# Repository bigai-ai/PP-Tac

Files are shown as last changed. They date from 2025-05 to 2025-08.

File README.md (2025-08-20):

# PP-Tac: Paper Picking Using Tactile Feedback in Dexterous Robotic Hands

[Pei Lin<sup>*</sup>](http://peilin-666.github.io/)<sup>1,2</sup>,
[YuZhe Huang<sup>*</sup>]<sup>1,3</sup>,
[Wanlin Li<sup>*</sup>](https://mrliwanlin.github.io/)<sup>1</sup>,
[Jianpeng Ma]<sup>1</sup>,
[Chenxi Xiao<sup>†</sup>](https://scholar.google.com/citations?hl=zh-CN&user=Qhiy3doAAAAJ)<sup>2</sup>,
[Ziyuan Jiao<sup>†</sup>](https://scholar.google.com/citations?user=YfWhJZoAAAAJ&hl=zh-CN&oi=ao)<sup>1</sup>

<sup>1</sup>Beijing Institute for General Artificial Intelligence,
<sup>2</sup>ShanghaiTech University,
<sup>3</sup>Beihang University

# R-Tac Sensor Guide
### Low-cost, 120fps, Round-shape Single-channel Vision-based Tactile Sensor
[[Project page]](https://peilin-666.github.io/projects/PP-Tac/)
[[Paper]](https://arxiv.org/abs/2504.16649)
[[Video Tutorial_Youtube]](https://www.youtube.com/watch?v=-npk0cRKWGI)
[[Video Tutorial_Bilibili]](https://www.bilibili.com/video/BV1pLKwzkEMb/?spm_id_from=333.337.search-card.all.click)

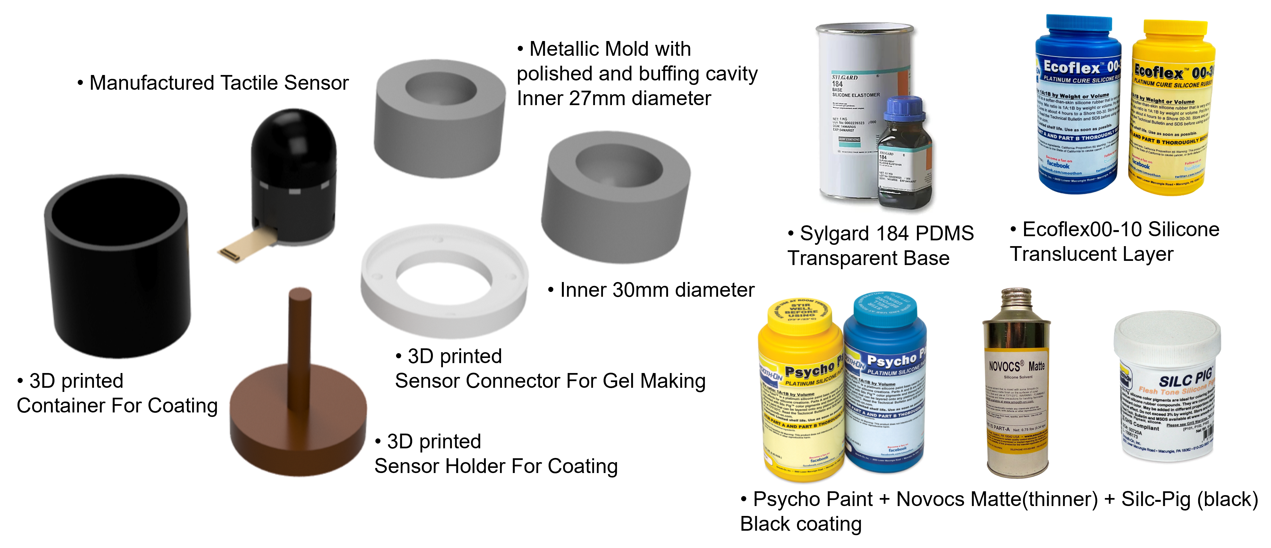
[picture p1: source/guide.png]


## CAD Models</a>
All CAD models can be downloaded and edited from [[onshape]](https://cad.onshape.com/documents/9472112f26da7f3a688b4739/w/3c5ca2de4889759493b1cc6c/e/c49e7e8ea4181ab75b1e7674)
(right click and copy link address to enter).<br>
3D printed files (print with supportings) can be found in [3Dprinting](Model/3Dprinting).

## Camera</a>
We use 120fps OV9281 Monochrome camera module which can be bought from [Taobao](https://item.taobao.com/item.htm?id=740654464379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) or [Amazon](https://www.amazon.co.uk/Global-Shutter-Camera-Detection-Modules-100-degrees/dp/B0D5SNTHSD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)

## PCBs</a>
The PCB files can be downloaded from [PCB](PCB/) and is powered by 5V.<br>
If you opt for white LED chips, it is recommended to select the 2835 package type and pay attention to the anode and cathode of the LED chips.<br>
<div style="display: flex; align-items: center;">
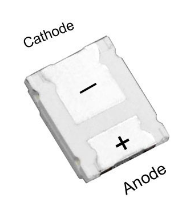
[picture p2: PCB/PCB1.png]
  
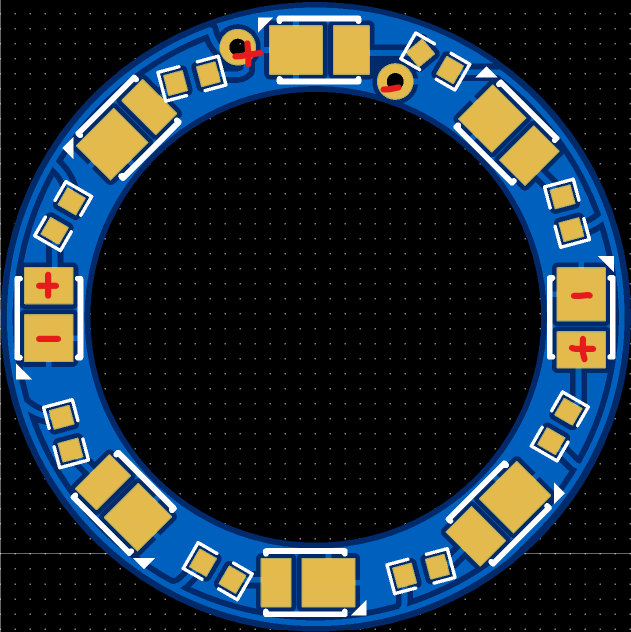
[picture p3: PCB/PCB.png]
  
</div>

## Diffuser Boards</a>
Diffuser patterns (.dxf) can be downloaded from [Diffuser](Model/Diffuser). It is recommended to laser-cut the [double-sided frosted one](https://detail.tmall.com/item.htm?id=550079594688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). You can also try 3D printing with white resin. <br>

## Metallic Mold</a>
The design files can be downloaded from [Mold](Model/MetalMold). Two molds are needed for PDMS casting (27mm diameter) and Silicone casting (30mm diameter). The mold is fabricated using stainless steel with polished and buffing cavity.<br>

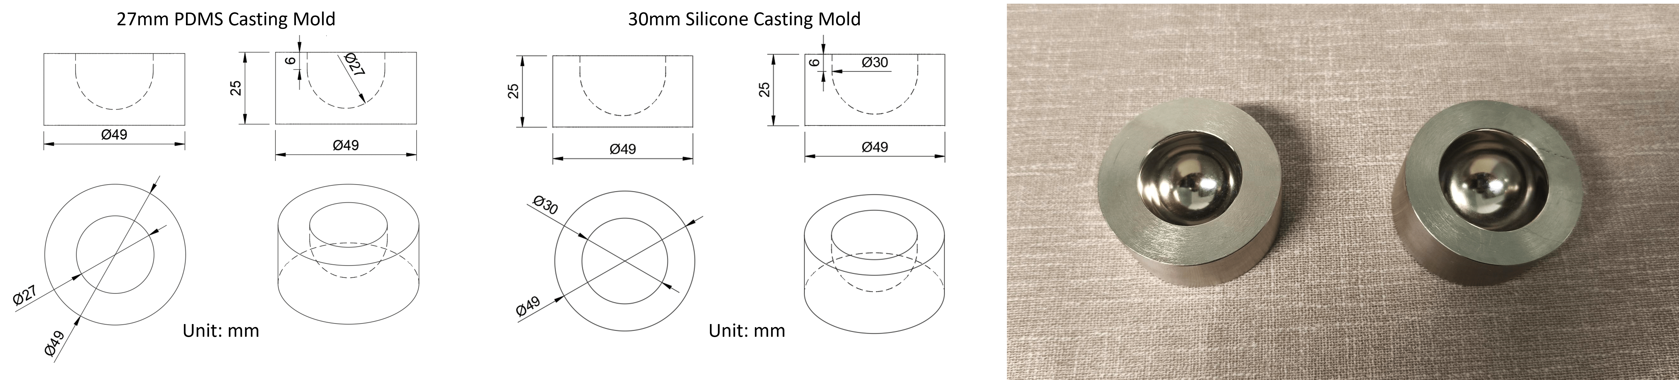
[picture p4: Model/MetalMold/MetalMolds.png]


## BOM</a>

| Component | Description | Remark |
|---|---|---|
| PDMS | Transparent base | [SYLGARD™ 184](https://www.dow.com/en-us/pdp.sylgard-184-silicone-elastomer-kit.01064291z.html#overview) |
| Silicone | Translucent layer | [Ecoflex™ 00-10](https://www.smooth-on.com/products/ecoflex-00-10/) |
| Black pigment | Coating colorant | [Silc Pig™](https://www.smooth-on.com/products/silc-pig/) |
| Coating | Coating layer | [Psycho Paint™](https://www.smooth-on.com/products/psycho-paint/) |
| Thinner | Coating layer thinner | [NOVOCS™ Matte](https://www.smooth-on.com/products/novocs/) |
| Release agent | Silicone release agent | [Ease Release™ 200](https://www.smooth-on.com/products/ease-release-200/) |
| Bolts | M2 * 4 & M1.6 * 5 & M3 *4 | bolts |
| Hot melt nuts | M2 * 2 * 3 | nuts |
| Soldering iron | Compatiable with above nuts | [Soldering Iron](https://item.taobao.com/item.htm?_u=i2jo70qs4f40&id=676644094694&spm=a1z09.2.0.0.32402e8dfa9bP4)|
| Scale | For silicone mixing | Electronic Scale |
| Tape | Double-sided tape | Tape |
| Stick | Stirring silicone | Small Wood Stick |
| Cup | Container for silicone | Disposable Cups |
| Sticker | Dust removal of silicone surface | [Sticker](https://item.taobao.com/item.htm?_u=i2jo70qsf114&id=561103645534&spm=a1z09.2.0.0.32402e8dfa9bP4)|
| Vacuum pump | Air degassing for silicone | [Vacuum Pump](https://detail.tmall.com/item.htm?id=593806957297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)|
| Other tools | Small scissor, tweezer, knife | Tools |

## Video Guide</a>
[[YouTube]](https://www.youtube.com/watch?v=-npk0cRKWGI)
[[Bilibili]](https://www.bilibili.com/video/BV1pLKwzkEMb/?spm_id_from=333.337.search-card.all.click)

# Sensor Calibration
**Recommended camera resolution: 640 * 480**
## 0. Camera Intrinsic Calibration</a>
Refer to [this website](https://github.com/dyfcalid/CameraCalibration/tree/master/IntrinsicCalibration) for intrinsic calibration.
## 1. Camera Extrinsic Calibration</a>
3D print the [calibration tools](Calibration/3Dprint): top, surrounding and 5 pins. Drill and clean the holes in the top model to ensure that pins can be inserted.<br>

In accordance with the hole index in the figure below and referring to the **capture name** in this [folder](Calibration/sensor1/calib_extrinsic), insert the five pins into the corresponding holes in one go. Subsequently, save and replace the existing images.
<div style="display: flex; align-items: center;">
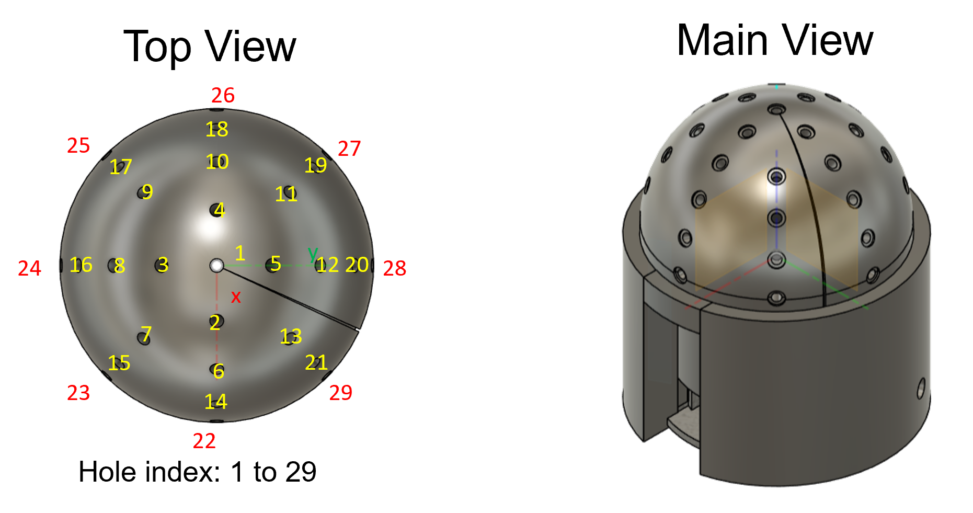
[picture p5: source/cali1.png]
  
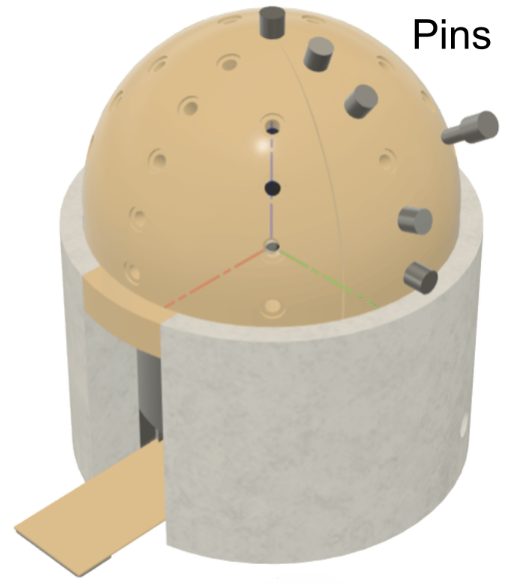
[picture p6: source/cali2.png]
  
</div>

run ./Calibration/1CameraExtrinsics.py and replace the **CAMERA_MATRIX** and **Distortion** with your own camera intrinsc parameters to obtain the camera extrinsics.

## 2. Obtain the Reference Depth Map</a>
run ./Calibration/2Reprojection.py to obtain the reference depth map and the mask center and radius.

## 3. Surface Reconstruction</a>
you can either directly run ./Calibration/3ShapeReconstruction_directuse.py to obtain the surface shape via the model we have trained using indenters 
<br>
or 
<br>
you can build a table by yourself using a single ball capture (press on the top middle area), by running ./Calibration/3SensorCalibration.py and ./Calibration/4ShapeReconstruction.py

## Acknowledgment</a>
[9DTact: A Compact Vision-Based Tactile Sensor for Accurate 3D Shape Reconstruction and Generalizable 6D Force Estimation](https://arxiv.org/abs/2308.14277), Lin et al., RAL 2023

## Reference
```
@article{lin2025pp,
  title={PP-Tac: Paper Picking Using Tactile Feedback in Dexterous Robotic Hands},
  author={Lin, Pei and Huang, Yuzhe and Li, Wanlin and Ma, Jianpeng and Xiao, Chenxi and Jiao, Ziyuan},
  journal={arXiv preprint arXiv:2504.16649},
  year={2025}
}
```

<!-- 
```
@INPROCEEDINGS{lin2025pp, 
    author={Lin, Pei and Huang, Yuzhe and Li, Wanlin and Ma, Jianpeng and Xiao, Chenxi and Jiao, Ziyuan},
    title     = {PP-Tac: Paper Picking Using Tactile Feedback in Dexterous Robotic Hands},
    booktitle = {Robotics Science and Systems (RSS)}, 
    year      = {2025}, 
} 
```
-->

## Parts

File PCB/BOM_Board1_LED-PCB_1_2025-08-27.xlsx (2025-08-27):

No. | Quantity | Comment | Designator | Footprint | Value | Manufacturer Part | Manufacturer | Supplier Part | Supplier
1 | 8 | HL-AM-2835H421W-S1-08-HR6(SDCM | LED1,LED2,LED3,LED4,LED5,LED6,LED7,LED8 | LED-SMD_L3.5-W2.8-RD |  | HL-AM-2835H421W-S1-08-HR6(SDCM | HONGLITRONIC(鸿利光电) | C516134 | LCSC
2 | 8 | 470Ω | R1,R2,R3,R4,R5,R6,R7,R8 | R0603 | 470Ω | 0603WAF4700T5E | UNI-ROYAL(厚声) | C23179 | LCSC

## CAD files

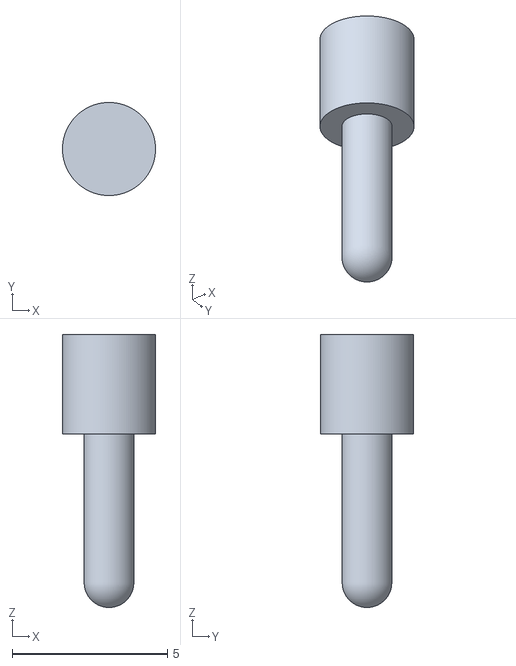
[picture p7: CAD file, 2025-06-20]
Calibration/3Dprint/calibration_5pins.stl
3.00 x 3.00 x 8.80

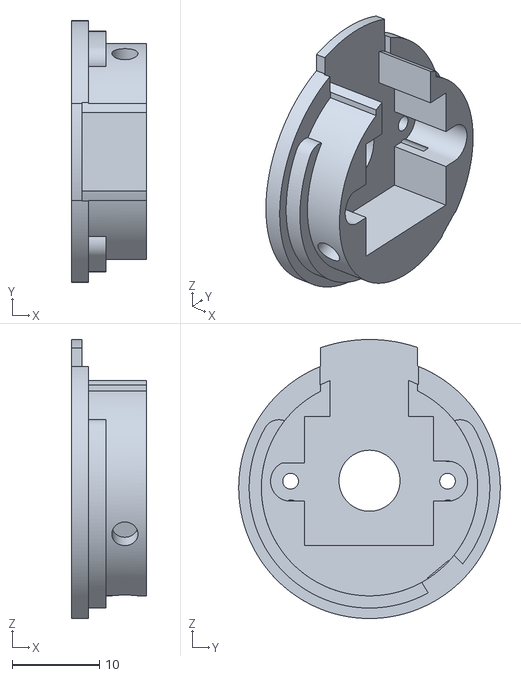
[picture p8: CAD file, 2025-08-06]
Model/3Dprinting/SensorBase.stl
8.65 x 30.0 x 32.0

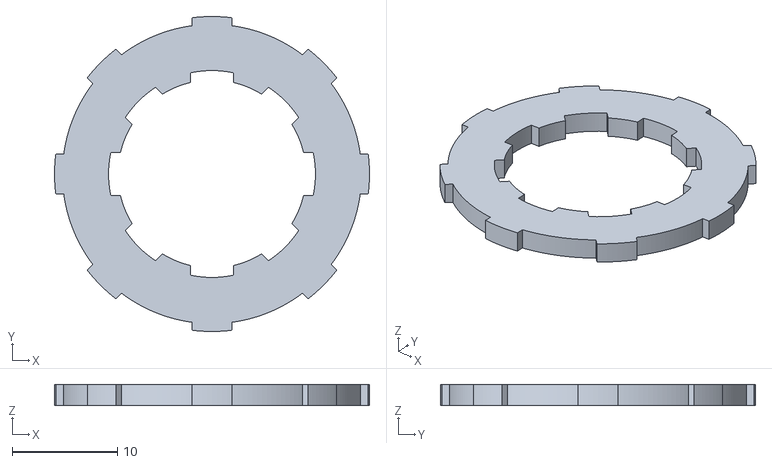
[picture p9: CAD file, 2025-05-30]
Model/Diffuser/diffuser.stl
30.0 x 30.0 x 2.00

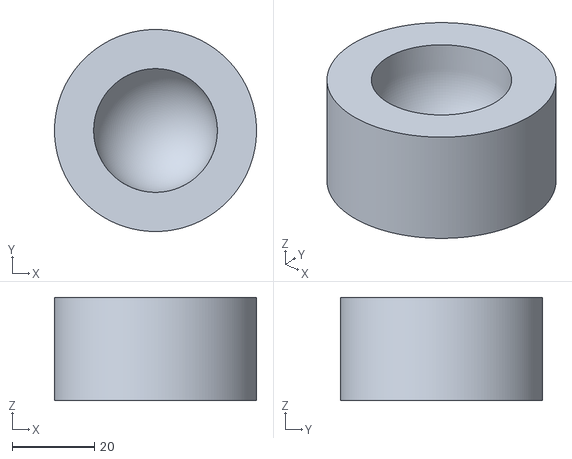
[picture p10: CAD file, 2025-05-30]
Model/MetalMold/30mmSiliconecasting.stl
49.0 x 49.0 x 25.0

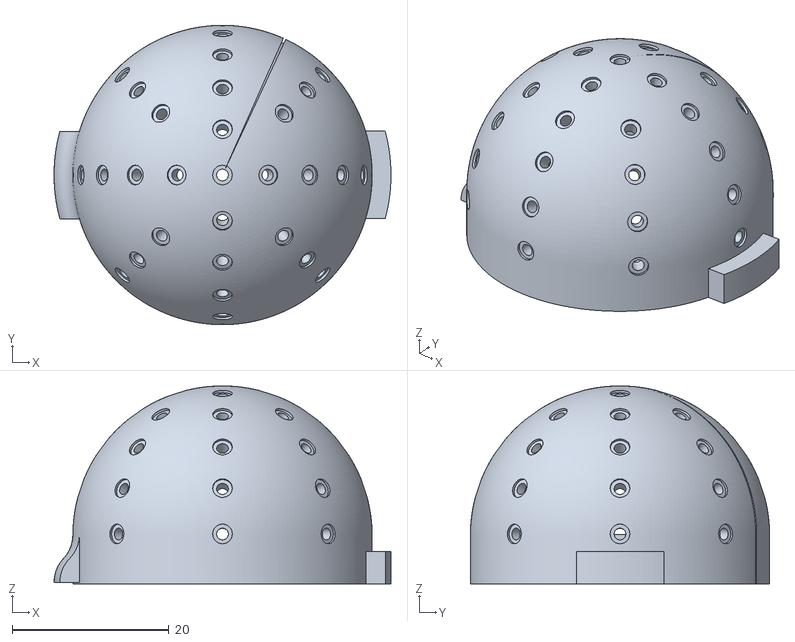
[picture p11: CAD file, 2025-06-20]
Calibration/3Dprint/calibration_top.stl
43.0 x 38.2 x 25.2

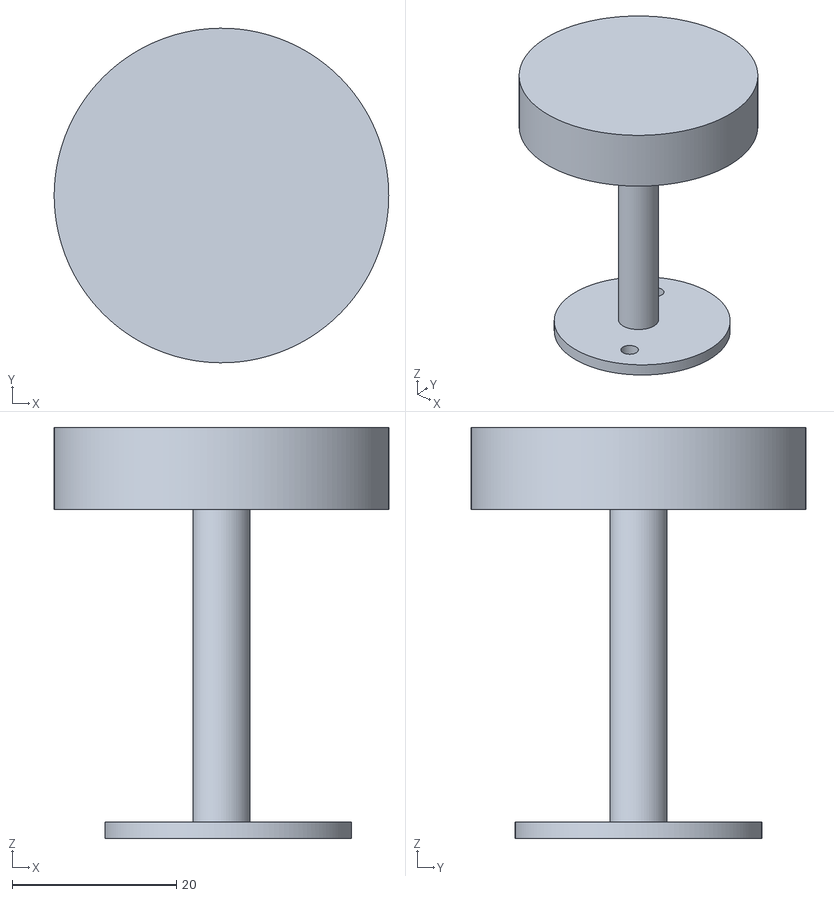
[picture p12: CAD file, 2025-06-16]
Model/3Dprinting/SensorHolderForCoating.stl
40.7 x 40.7 x 50.0

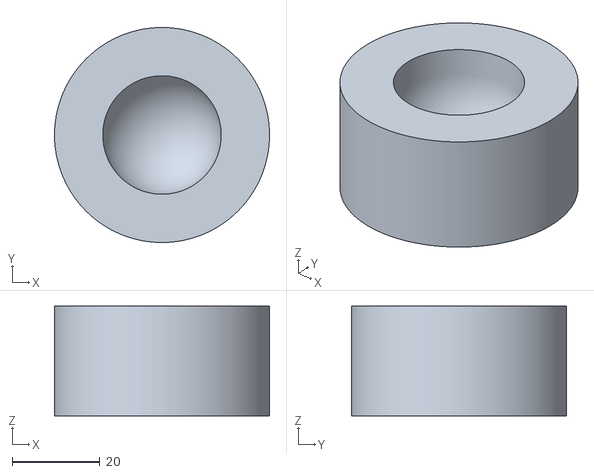
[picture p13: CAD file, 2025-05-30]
Model/MetalMold/27mmPDMScasting.stl
49.0 x 49.0 x 25.0

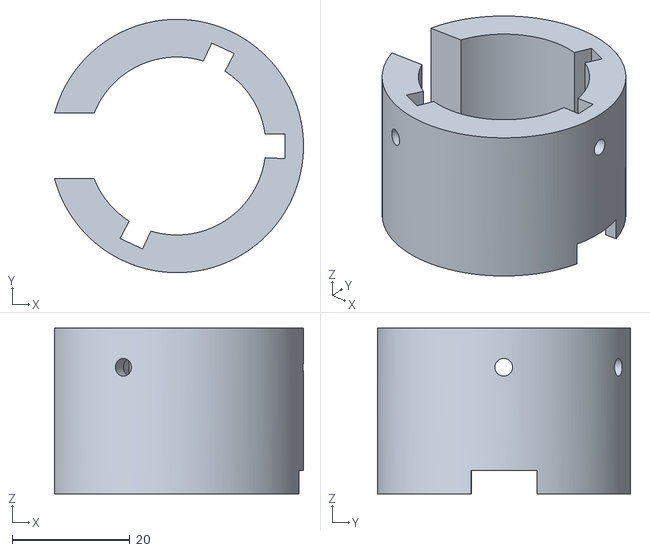
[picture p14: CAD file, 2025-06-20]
Calibration/3Dprint/calibration_surrounding.stl
42.3 x 43.0 x 28.2

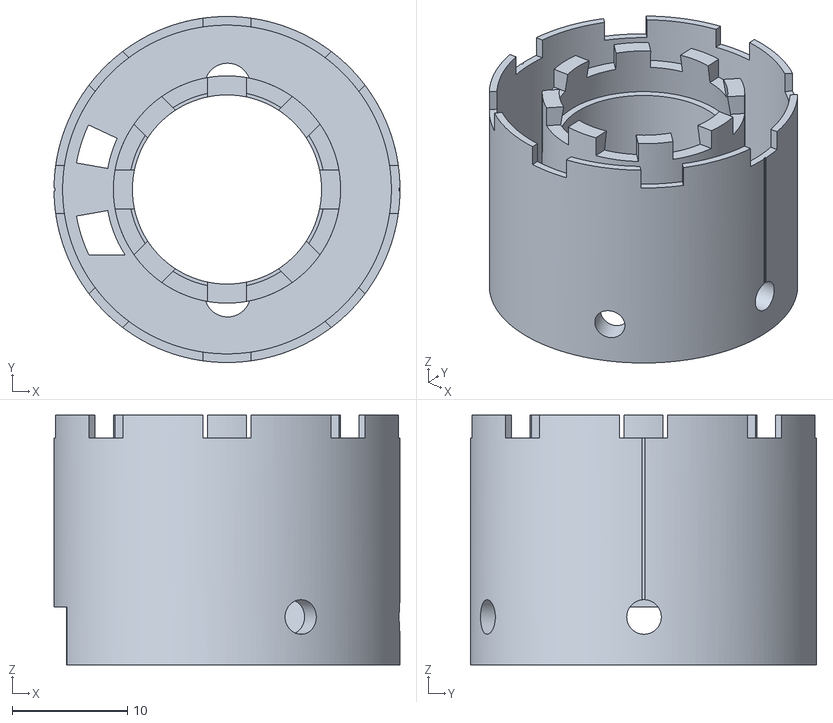
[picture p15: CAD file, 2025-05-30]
Model/3Dprinting/SensorShell.stl
30.0 x 30.0 x 21.6

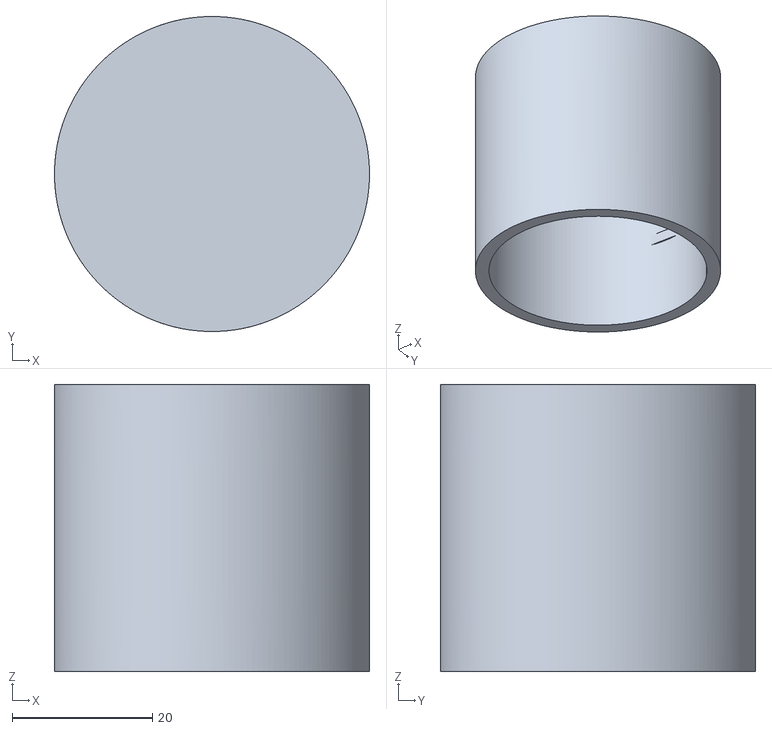
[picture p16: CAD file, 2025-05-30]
Model/3Dprinting/ContainerForCoating.stl
45.0 x 45.0 x 41.0

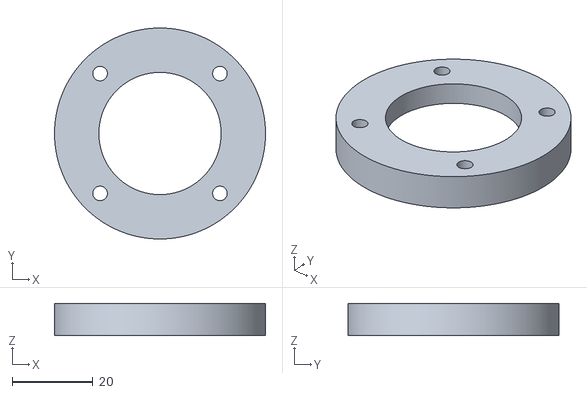
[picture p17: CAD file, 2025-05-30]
Model/3Dprinting/SensorConnectorForGelMaking.stl
52.1 x 52.1 x 8.00

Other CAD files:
Model/Diffuser/diffuser.dxf

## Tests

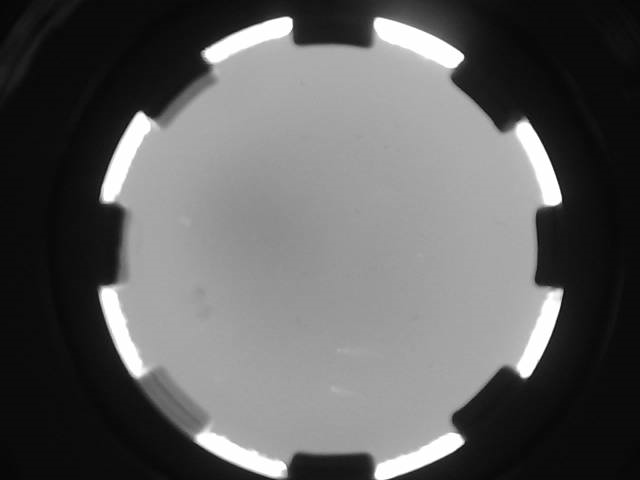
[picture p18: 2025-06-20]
Calibration/sensor1/calib_extrinsic/ref.png

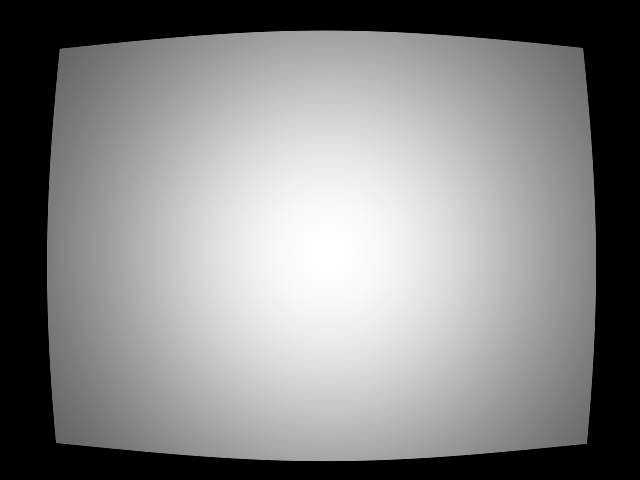
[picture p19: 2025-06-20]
Calibration/sensor1/ref_depth.png
